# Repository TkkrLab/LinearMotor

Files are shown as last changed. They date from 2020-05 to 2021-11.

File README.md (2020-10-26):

# DIY Ironless Linear Motor
Brushless DC (BLDC) motors constist of a stator and a rotor, which produce a rotational torque when powered. A linear motor is essentially a BLDC motor which has been folded open and produces a linear force by applying current to the different phases. This causes the [forcer](#forcer) (rotor) to move along a [magnetic track](#magnetic-track) (stator).
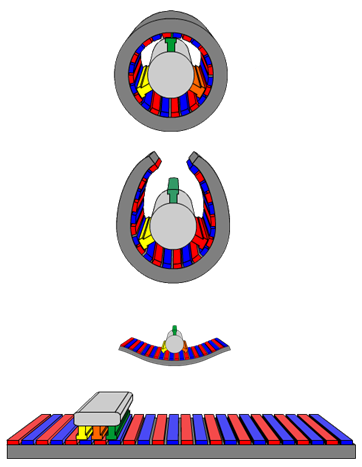
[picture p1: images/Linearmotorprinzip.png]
LinearMotorPrincipal


## Linear Motor basics
As explained a linear motor is a flattened BLDC motor. There are several different types, each having its own advantages and disadvantages. We decided to go with an ironless linear motor.
An ironless linear motor has two main components:
* A magnetic track composed of two metal plates with magnets attached and a seperator / spacer. 
* A forcer composed of 3 copper coils, an aluminium housing, wiring and epoxy.
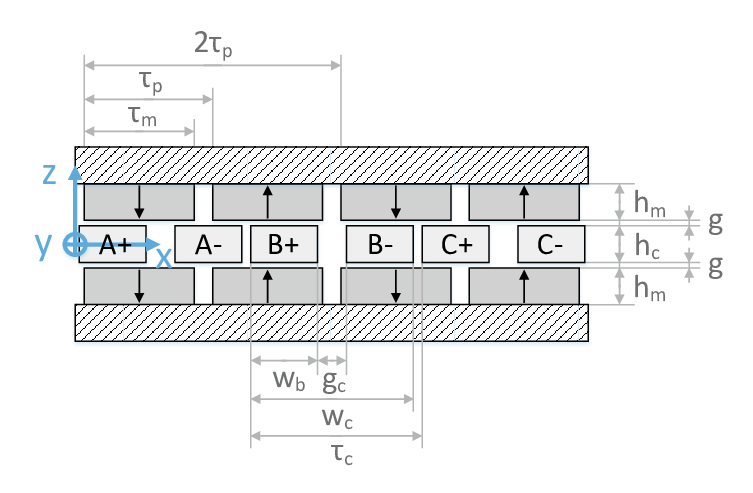
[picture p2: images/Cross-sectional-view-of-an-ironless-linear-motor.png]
CrossSection


### Magnetic Track
To get the correct spacing we take a look at a BLDC, in this case a three phase two pole motor.
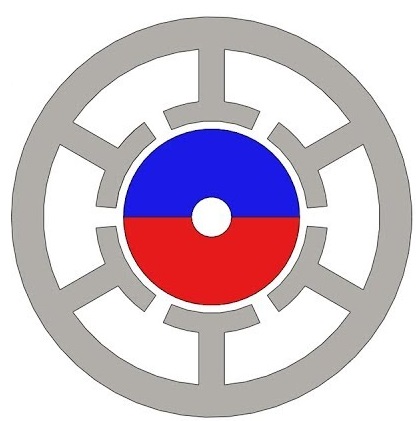
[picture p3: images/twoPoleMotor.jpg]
Three phase two pole motor


During rotation one of the phases of the motor will move from a positive polarity (+) to the negative polarity (-) and back to positive. The other two phases have a 120° offset from this phase, but for now lets focus on just the one phase. This translation in polarity means that we now know the spacing between magnets of the same polarity => 360° rotation, or 3* distance between coils(coil spacing). To get the coil spacing we take a look at what coils we have available.

The coils that we purchased were produced specifically for linear motors, they have a size of 25.5*14mm. Since we also want to add watercooling channels between the coils we decided on a spacing of 18mm. If you do not wish to add watercooling we would recommend putting the coils as close together as possible.

If we apply these values we would have a magnet with positive polarity at 0, negative polarity at 27mm and positive again at 54mm. Even though this would work, the motor will not be very powerfull. This can be improved by adding more pole pairs to the motor. You can keep adding adding pole pairs according to the following formula until you reach a magnet spacing / size suitable for your motor:  
Formula  
You can also decide on a magnet spacing first and calculate the coil spacing accordingly.

### Forcer
As previously mentioned we want to add watercooling to our linear motor so we can put more current into the coils without overheating the system. This adds some more complexity to the design of the forcer. 
For more details on the design check out [Version 1](/Solidworks/V1/README.md) and [Version 2 Watercooled](/Solidworks/V2_Watercooled/README.md)

There are some companies that sell coils made to specifications. We got ours from [JHCoils](https://www.jhcoils.com/), but if you are up to it you can always wind your own. If you decide to buy your coils, just keep in mind that you will have to pay extra if they do not have the required tooling available (So ask which sizes they have available already and pick one of those).
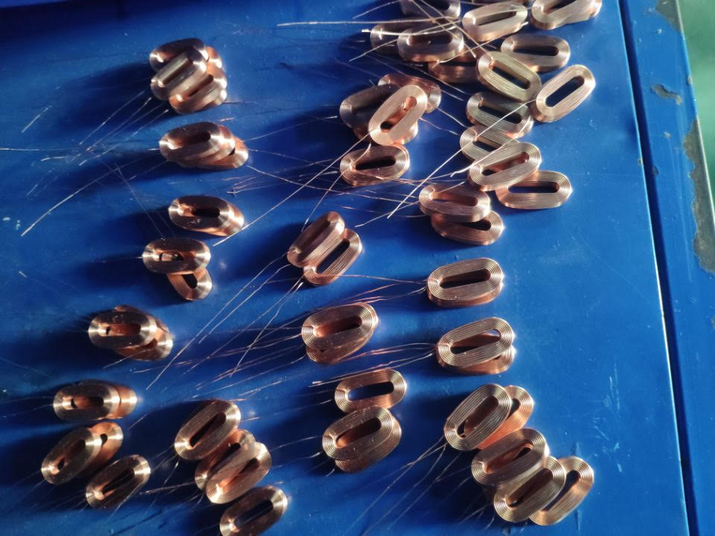
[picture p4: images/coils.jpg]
Coils


#### Coil specs
dimensions: 25.5*14 mm  
wire: 0.4mm

## Commutation
Commutation is the process of switching current in the motor phases to generate motion. Our ironless linear motors is based on a three phase motor design. There are several different ways to commutate a three phase motor, of which sinusoidal control is the most efficient and most commonly used in the higher-end motor drives. 

In sinusoidal commutation, all three wires are permanently energized with a sinusoidal current that is 120 degrees apart on each phase. This has the effect of creating a North/South magnetic field that rotates inside the motor cage. As shown in the figure below:  
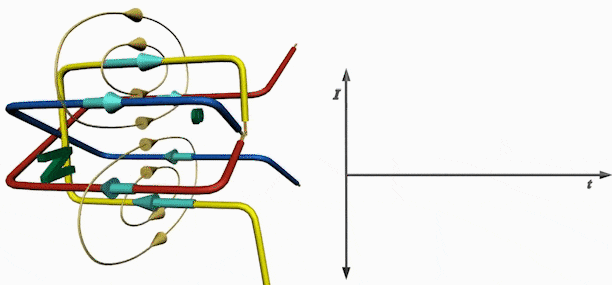
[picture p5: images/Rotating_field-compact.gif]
Commutation


If a magnet is placed on a rotor inside this cage, its North and South poles will be pulled towards the South and North poles of the rotating field. Assuming for a moment that the magnetis field rotation is paused, we can see the effect of the pull on the magnet at different angular position relative to the rotating field.

### FOC (Field Oriented Control)
...TODO...  
(https://www.roboteq.com/technology/field-oriented-control)

### Motor Drive
To drive our motor we are using a [TMC4671](https://www.trinamic.com/products/integrated-circuits/details/tmc4671-es/) controller from [Trinamic](#sponsors)

We use this drive specifically because it has hardware FOC (Field Oriented Control). The TMC4671 [datasheet](https://www.trinamic.com/fileadmin/assets/Products/ICs_Documents/TMC4671_datasheet_v1.06.pdf)  explains very well what FOC is exactly, so please check it out.

### Motor Initialization
...TODO...

__So why make our own?__
Simply, just because we can! And its awesome to learn about new stuff.

We do wish to mention [Vulcaman's](https://www.instructables.com/id/DIY-IRONLESS-LINEAR-SERVO-MOTOR/) motor build. This version is based on a simple L6234 motor controller IC and implements a basic sinusoidal commutation.

## Sponsors
We would like to thank our Trinamic for providing us with a TMC4671 evaluation kit.
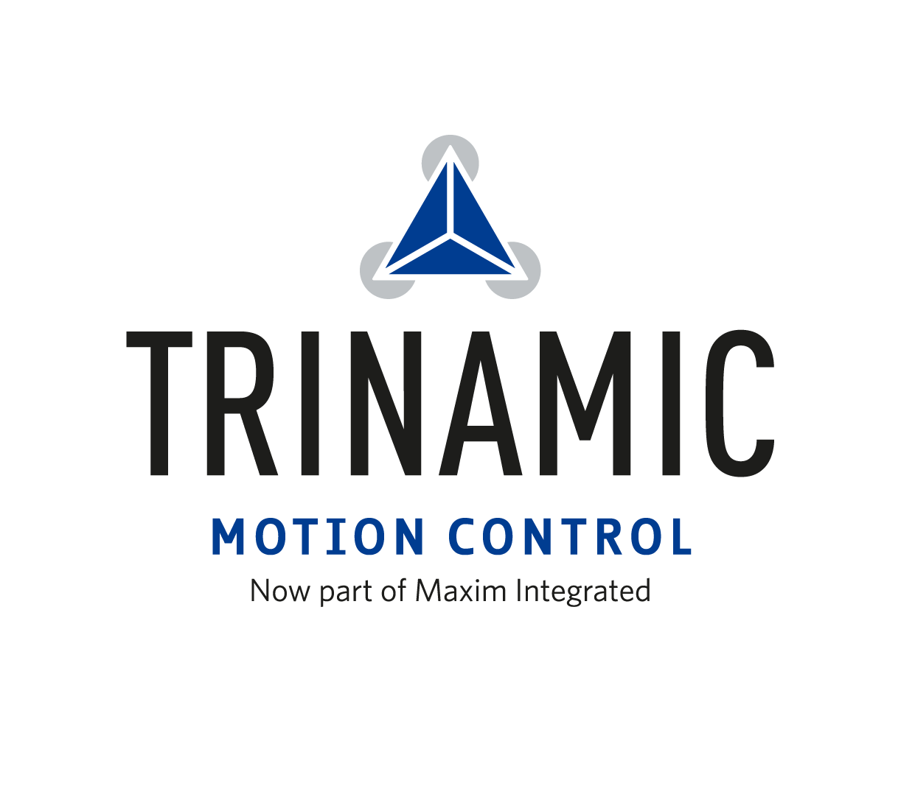
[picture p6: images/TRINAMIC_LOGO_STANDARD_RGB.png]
Trinamic


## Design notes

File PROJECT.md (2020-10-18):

---
title: "DIY Ironless Linear Motor"
date: 2020-10-03
thumbnail: "https://raw.githubusercontent.com/TkkrLab/LinearMotor/master/images/IMG_20200922_221401.jpg"
---

# DIY Ironless Linear motor
---TODO/Work in progress---

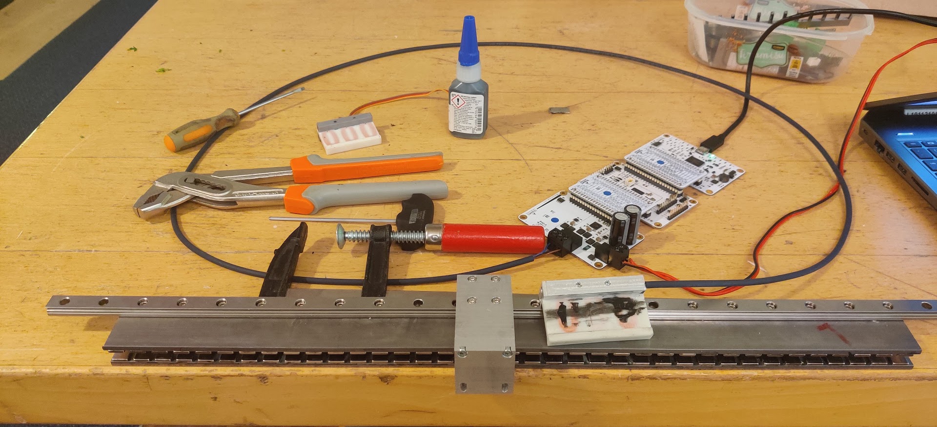
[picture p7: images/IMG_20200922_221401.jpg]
LinearMotor / LinearMotor


Check out github repository [github](https://github.com/TkkrLab/LinearMotor).

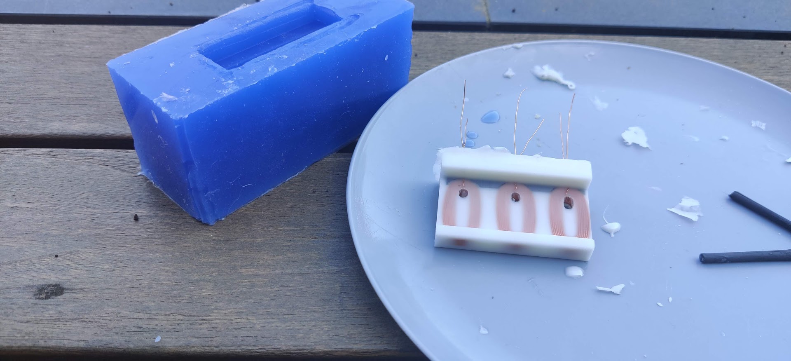
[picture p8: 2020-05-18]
images/forcer.jpg

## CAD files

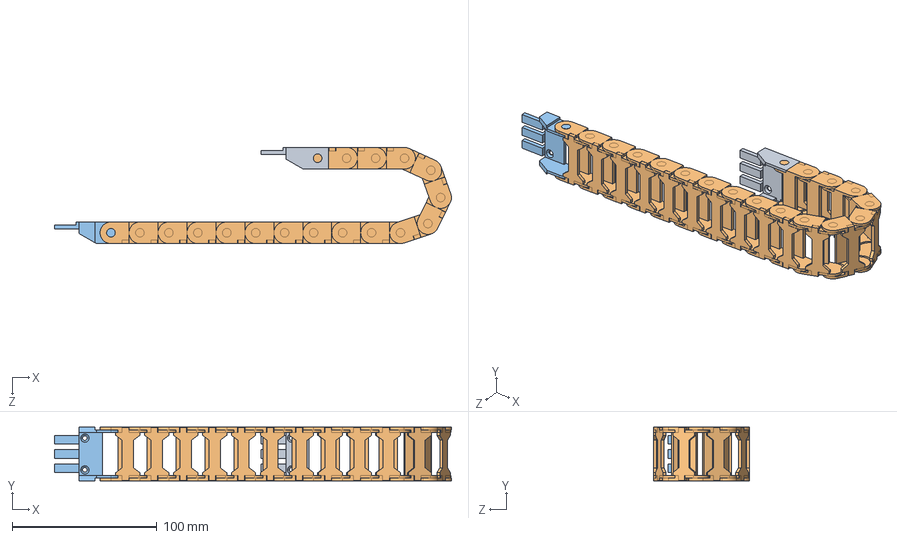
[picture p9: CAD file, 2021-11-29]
Solidworks/V2_Watercooled/Igus/chain.SLDASM
274.2 x 37.3 x 66.5 mm
0_36m_B07_30_018_0___060_30_12PZ_A1_3
0_36m_B07_30_018_0___060_30_12PZ_A1_4 x 17
0_36m_B07_30_018_0___060_30_12PZ_A1_2

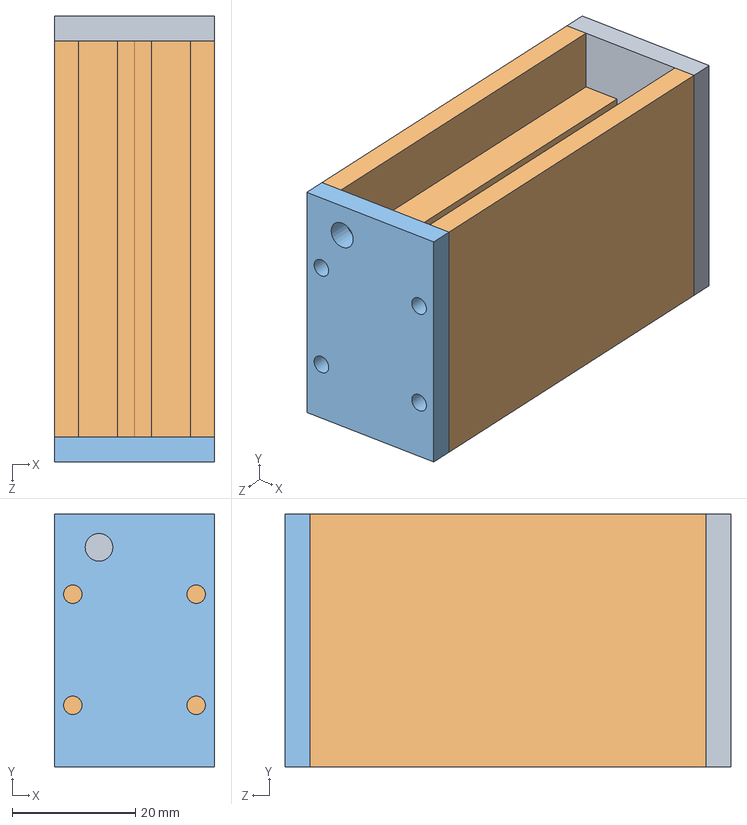
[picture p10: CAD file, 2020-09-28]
Solidworks/V2_Watercooled/CastingMould/mould.SLDASM
26.0 x 41.0 x 72.2 mm
backWall
sideWall x 2
frontWall

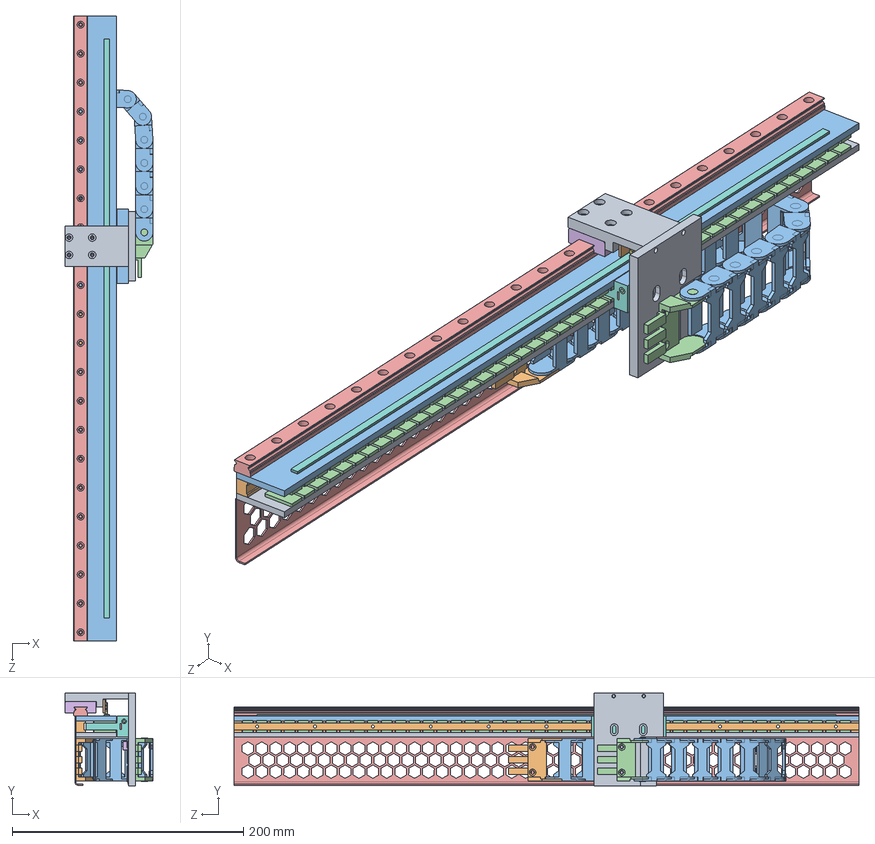
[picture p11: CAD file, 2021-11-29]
Solidworks/V2_Watercooled/LinearMotorAssembly.SLDASM
76.0 x 80.0 x 540.0 mm
enclosure_bottom
enclosure_Middle
enclosure_top
magnet_2mm x 88
MSA_012_SNS_P_MA_00
R0442_size12
RLC_3D
MS05_B-L500
connector_bracket_p1
RLC_pcb
forcer
M4 Set Screw (With Configs) x 3
spool holder
PVATube_Forcer_CoolingChannel x 2
spool x 3
forcer_printed
connector_bracket_p2
0_36m_B07_30_018_0___060_30_12PZ_A1_3
0_36m_B07_30_018_0___060_30_12PZ_A1_4 x 17
0_36m_B07_30_018_0___060_30_12PZ_A1_2
chainguide
tmc4670+tmc6100-bob

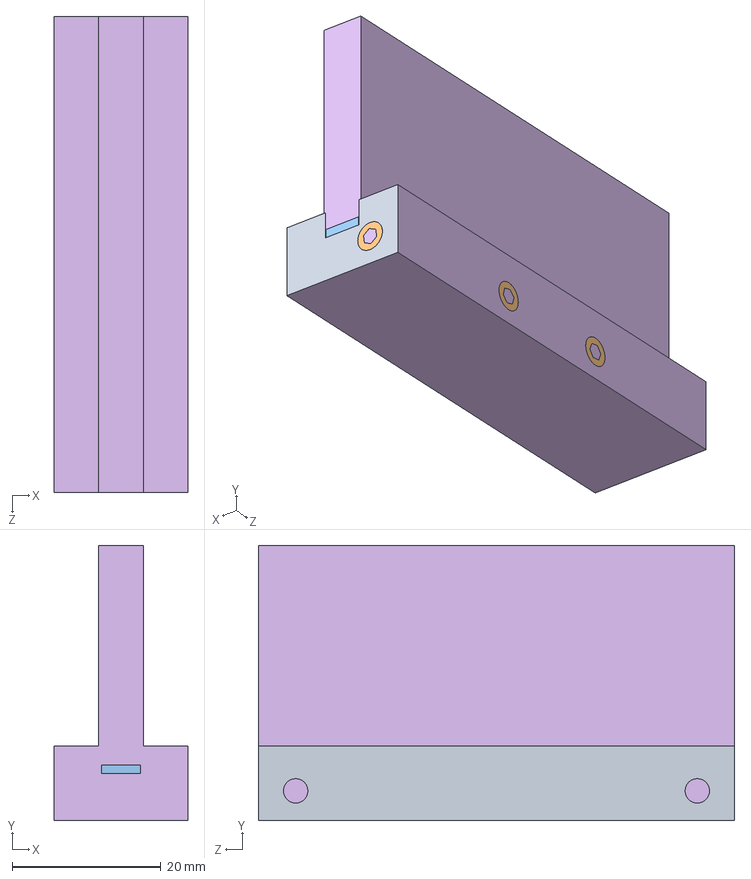
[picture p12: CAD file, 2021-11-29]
Solidworks/V2_Watercooled/forcer_assembly.SLDASM
18.0 x 37.0 x 64.0 mm
forcer
M4 Set Screw (With Configs) x 3
spool holder
PVATube_Forcer_CoolingChannel x 2
spool x 3

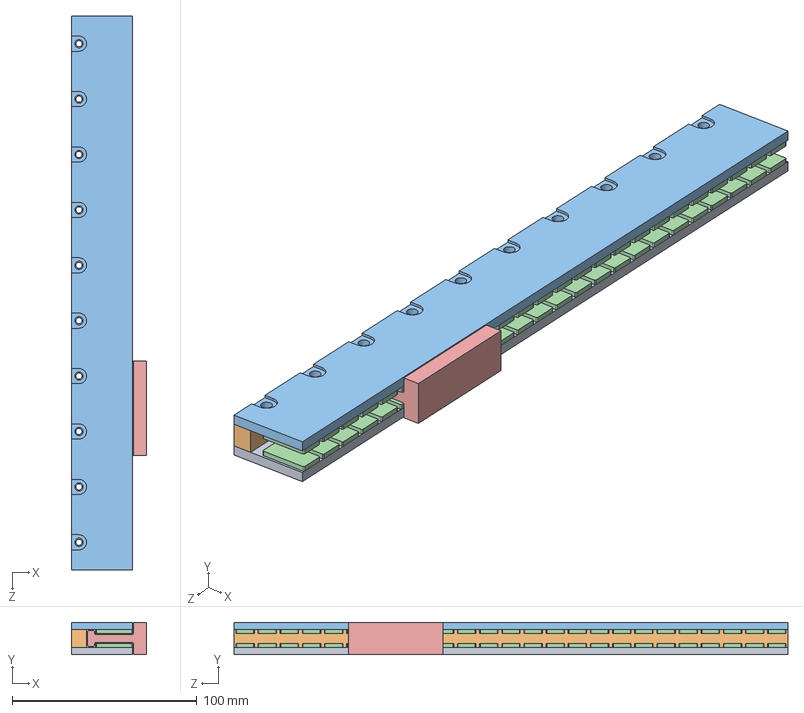
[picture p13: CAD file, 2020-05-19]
Solidworks/V1/LinearMotorAssembly.SLDASM
40.5 x 17.5 x 300.0 mm
enclosure_bottom
enclosure_Middle
enclosure_top
magnet_2mm x 50
forcer_part1

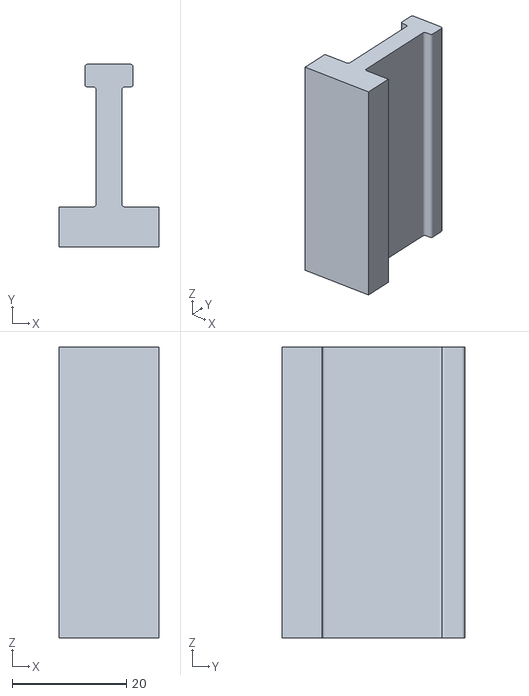
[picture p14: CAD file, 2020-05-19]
3d print STL/forcer_part1.STL
17.5 x 32.0 x 51.0

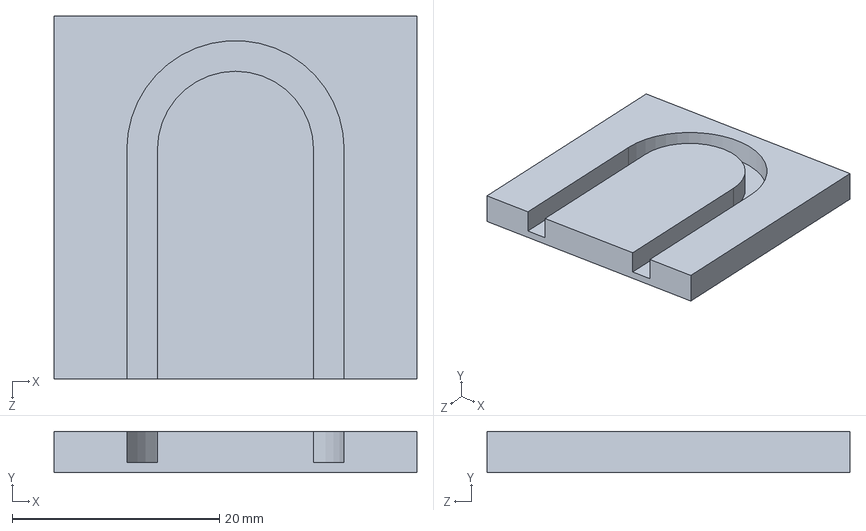
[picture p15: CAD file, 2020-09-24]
Solidworks/pva_forming_tool.SLDPRT
35.0 x 4.00 x 35.0 mm

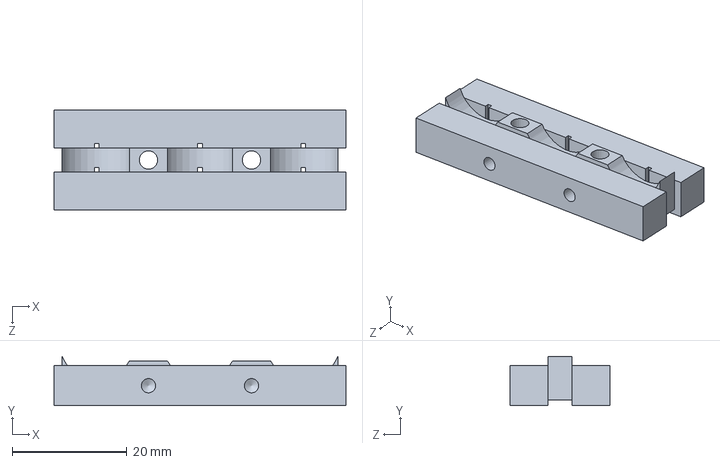
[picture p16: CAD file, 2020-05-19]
Solidworks/V1/forcer_part2.SLDPRT
51.0 x 8.64 x 17.5 mm

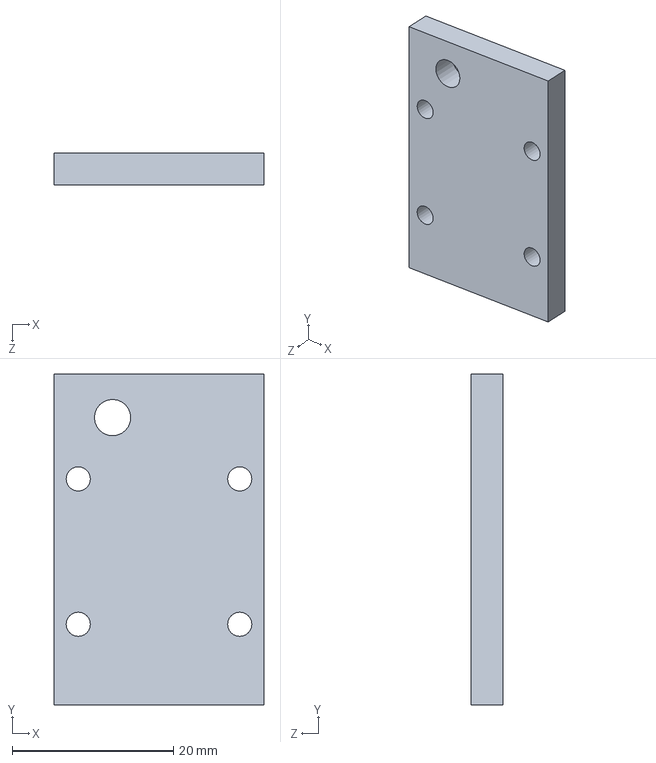
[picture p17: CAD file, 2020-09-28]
Solidworks/V2_Watercooled/CastingMould/frontWall.SLDPRT
26.0 x 41.0 x 4.00 mm

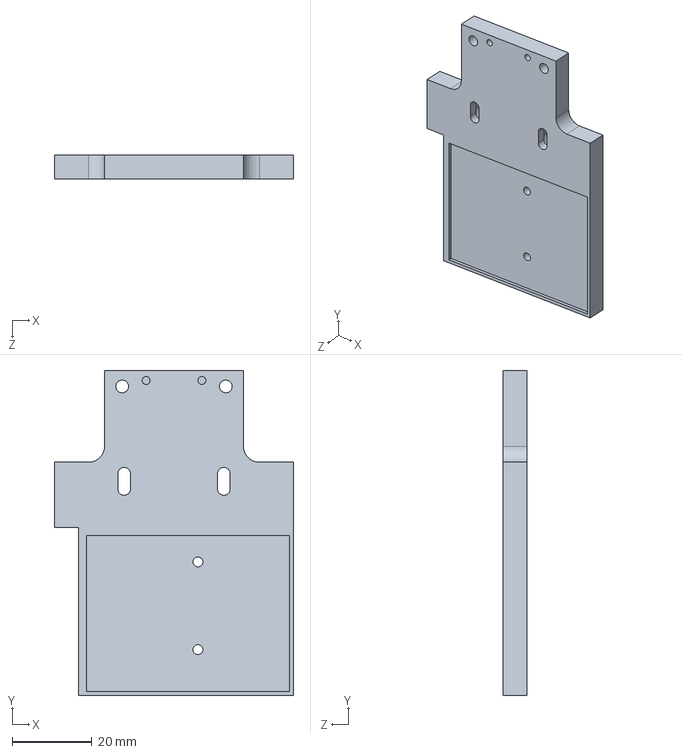
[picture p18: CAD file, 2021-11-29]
Solidworks/V2_Watercooled/connector_bracket_p2.SLDPRT
60.0 x 81.5 x 6.00 mm

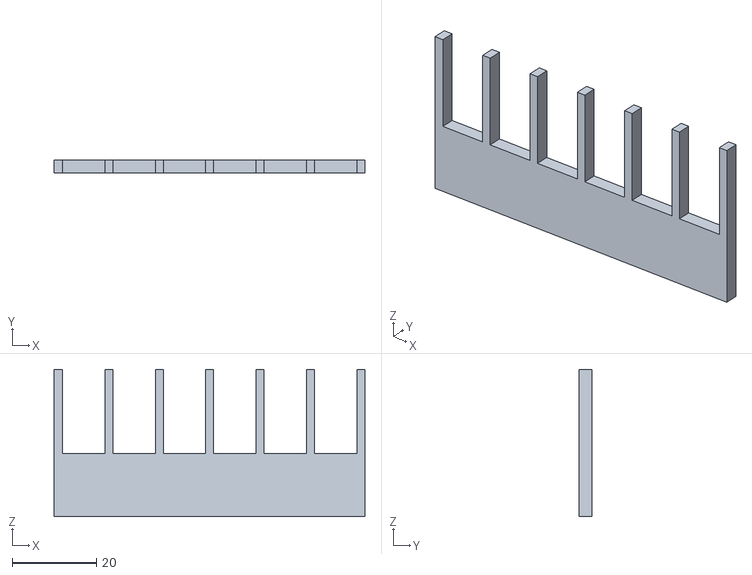
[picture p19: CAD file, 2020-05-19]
3d print STL/magnet_spacer.STL
74.0 x 3.00 x 35.0

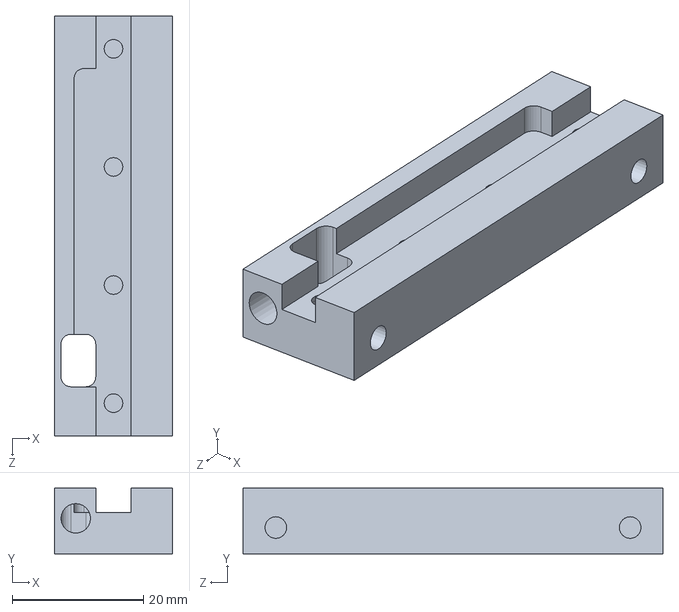
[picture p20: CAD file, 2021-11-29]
Solidworks/V2_Watercooled/forcer.SLDPRT
18.0 x 10.0 x 64.0 mm

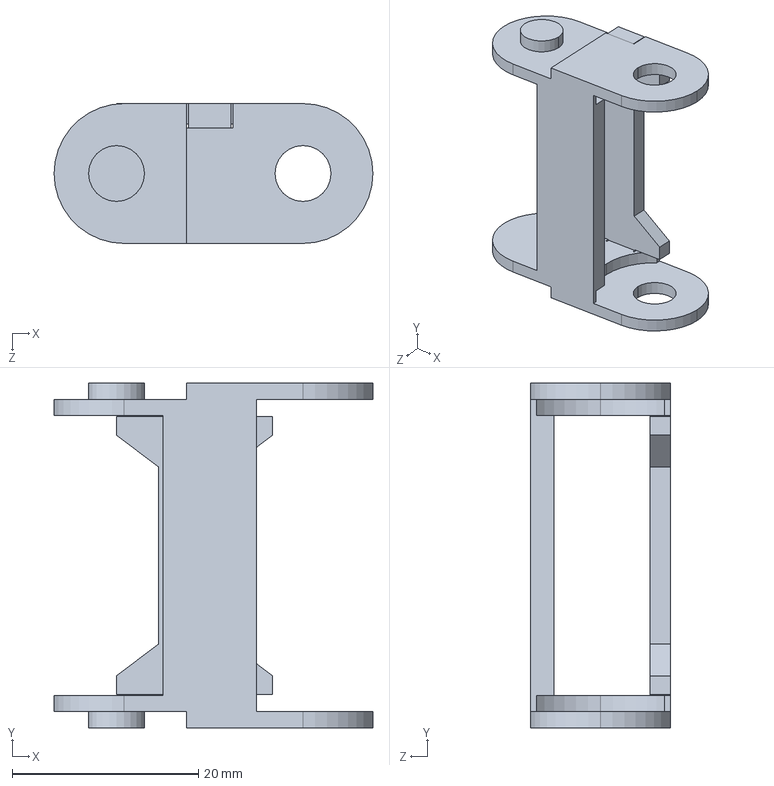
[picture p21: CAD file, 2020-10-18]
Solidworks/V2_Watercooled/Igus/0_36m_B07_30_018_0___060_30_12PZ_A1_4.SLDPRT
34.2 x 37.0 x 15.0 mm

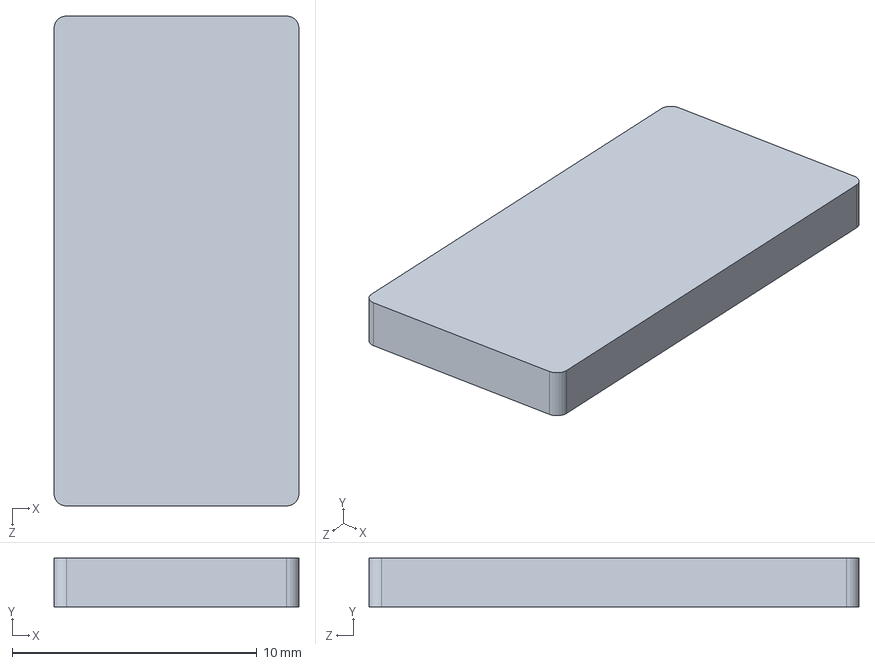
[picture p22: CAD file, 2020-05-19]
Solidworks/V1/magnet_2mm.SLDPRT
10.0 x 2.00 x 20.0 mm

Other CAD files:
Solidworks/V1/magnet_spacer.SLDPRT
3d print STL/forcer_part2.STL
Solidworks/V2_Watercooled/CastingMould/backWall.SLDPRT
Solidworks/V2_Watercooled/enclosure_top.SLDPRT
Solidworks/V1/enclosure_Middle.SLDPRT
Solidworks/V1/enclosure_bottom.SLDPRT
Solidworks/V1/enclosure_top.SLDPRT
Solidworks/V1/forcer_part1.SLDPRT
Solidworks/V2_Watercooled/CastingMould/sideWall.SLDPRT
Solidworks/V2_Watercooled/CoolingChannel.SLDPRT
Solidworks/V2_Watercooled/Igus/0_36m_B07_30_018_0___060_30_12PZ_A1_2.SLDPRT
Solidworks/V2_Watercooled/Igus/0_36m_B07_30_018_0___060_30_12PZ_A1_3.SLDPRT
Solidworks/V2_Watercooled/Igus/chainpath.SLDPRT
Solidworks/V2_Watercooled/M4 Set Screw.SLDPRT
Solidworks/V2_Watercooled/MS05B-L500.SLDPRT
Solidworks/V2_Watercooled/MSA_012_SNS_P_MA_00.SLDPRT
Solidworks/V2_Watercooled/R0442_size12.SLDPRT
Solidworks/V2_Watercooled/RLC2HD.SLDPRT
Solidworks/V2_Watercooled/RLC2HD_pcb.SLDPRT
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

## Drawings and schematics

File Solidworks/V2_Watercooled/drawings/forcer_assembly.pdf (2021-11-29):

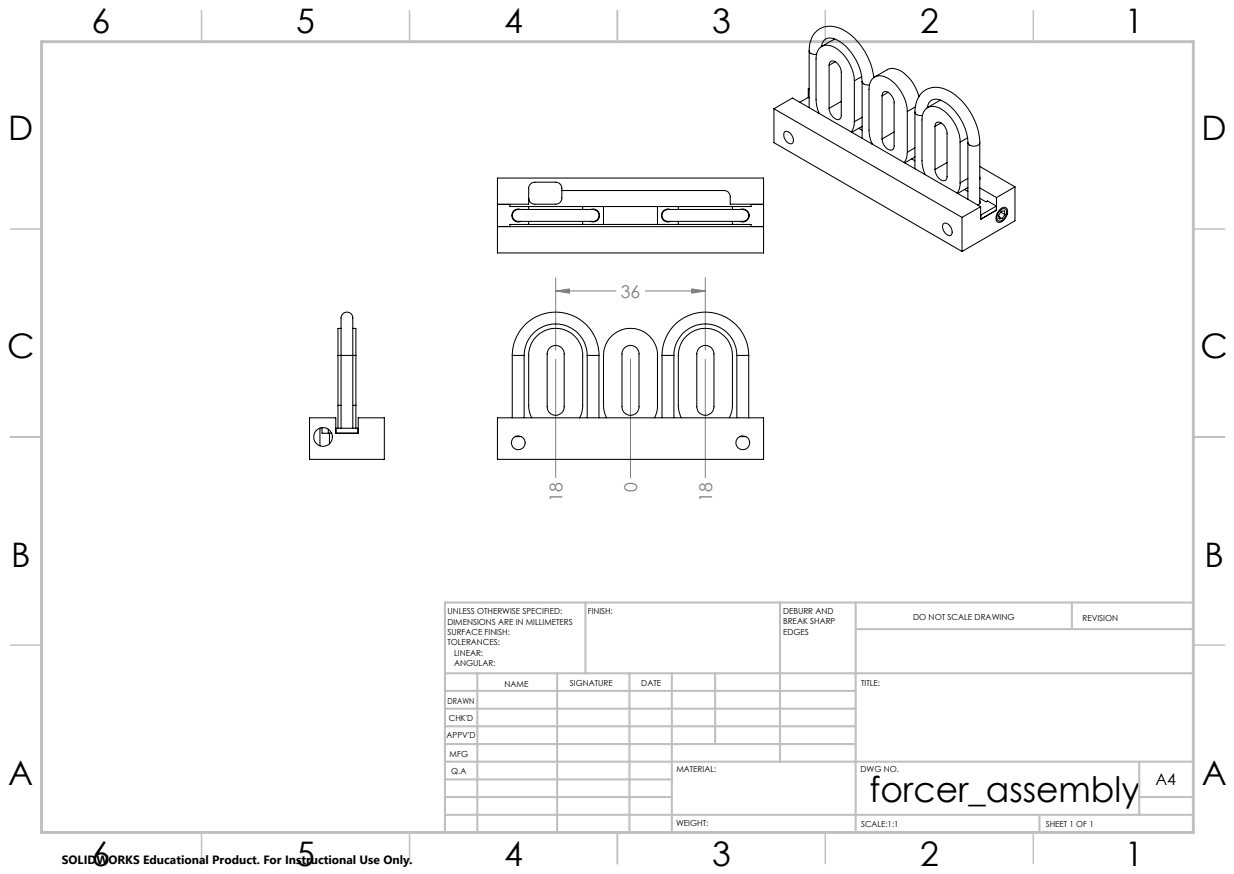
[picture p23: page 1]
FINISH:; DEBURR AND; BREAK SHARP; DO NOT SCALE DRAWING; REVISION; SCALE:1:1; SHEET 1 OF 1

UNLESS OTHERWISE SPECIFIED:
DIMENSIONS ARE IN MILLIMETERS
SURFACE FINISH:
TOLERANCES:
LINEAR:
ANGULAR:

NAME | SIGNATURE | DATE | | | | TITLE:

DRAWN
CHK'D
APPV'D
MFG
Q.A | | | | MATERIAL: | DWG NO. forcer_assembly | A4

SOLIDWORKS Educational Product. For Instructional Use Only.

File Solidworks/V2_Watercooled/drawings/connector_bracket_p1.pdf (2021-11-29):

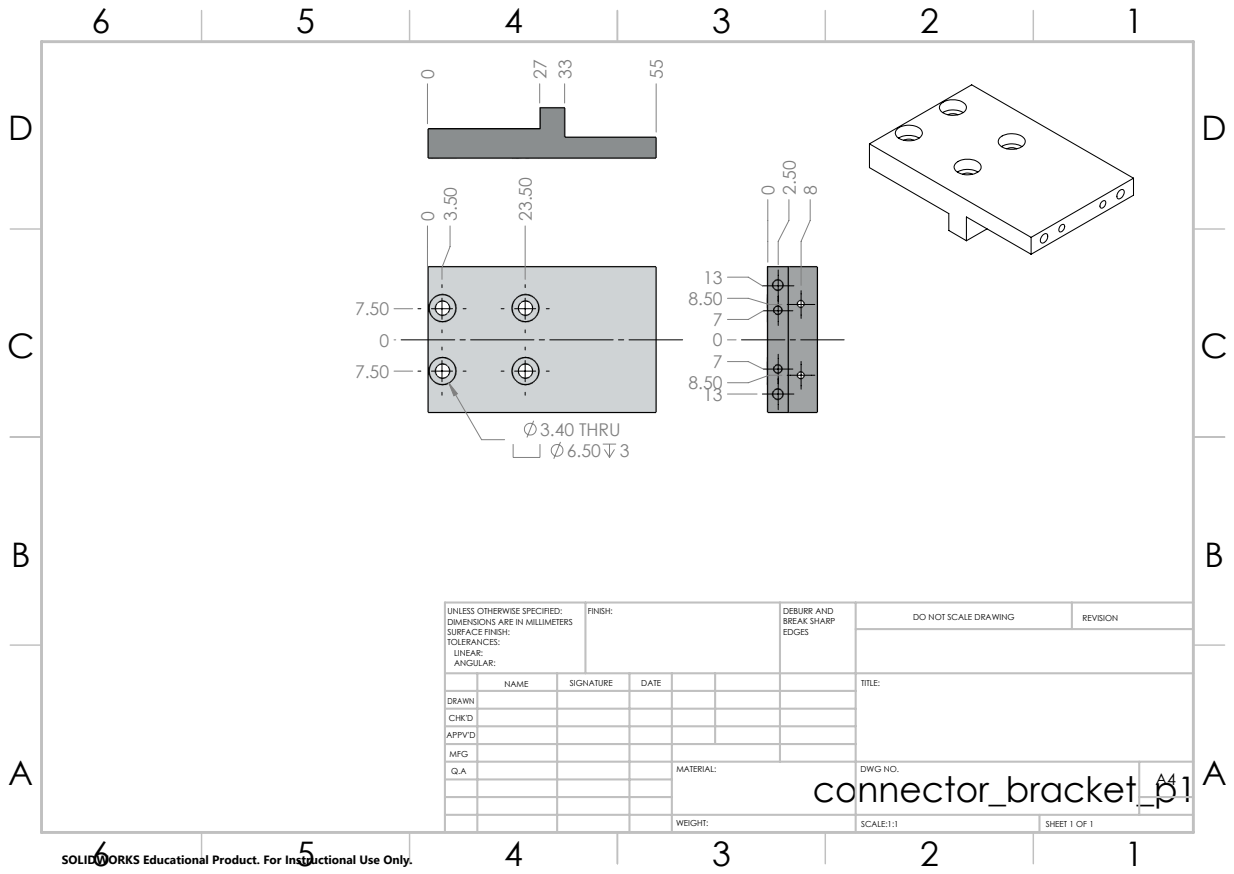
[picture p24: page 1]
3.40 THRU 6.50 3; FINISH:; DEBURR AND; BREAK SHARP; DO NOT SCALE DRAWING; REVISION; SCALE:1:1; SHEET 1 OF 1

UNLESS OTHERWISE SPECIFIED:
DIMENSIONS ARE IN MILLIMETERS
SURFACE FINISH:
TOLERANCES:
LINEAR:
ANGULAR:

NAME | SIGNATURE | DATE | | | | TITLE:

DRAWN
CHK'D
APPV'D
MFG
Q.A | | | | MATERIAL: connector_bracket_p1 | DWG NO. | A4

SOLIDWORKS Educational Product. For Instructional Use Only.

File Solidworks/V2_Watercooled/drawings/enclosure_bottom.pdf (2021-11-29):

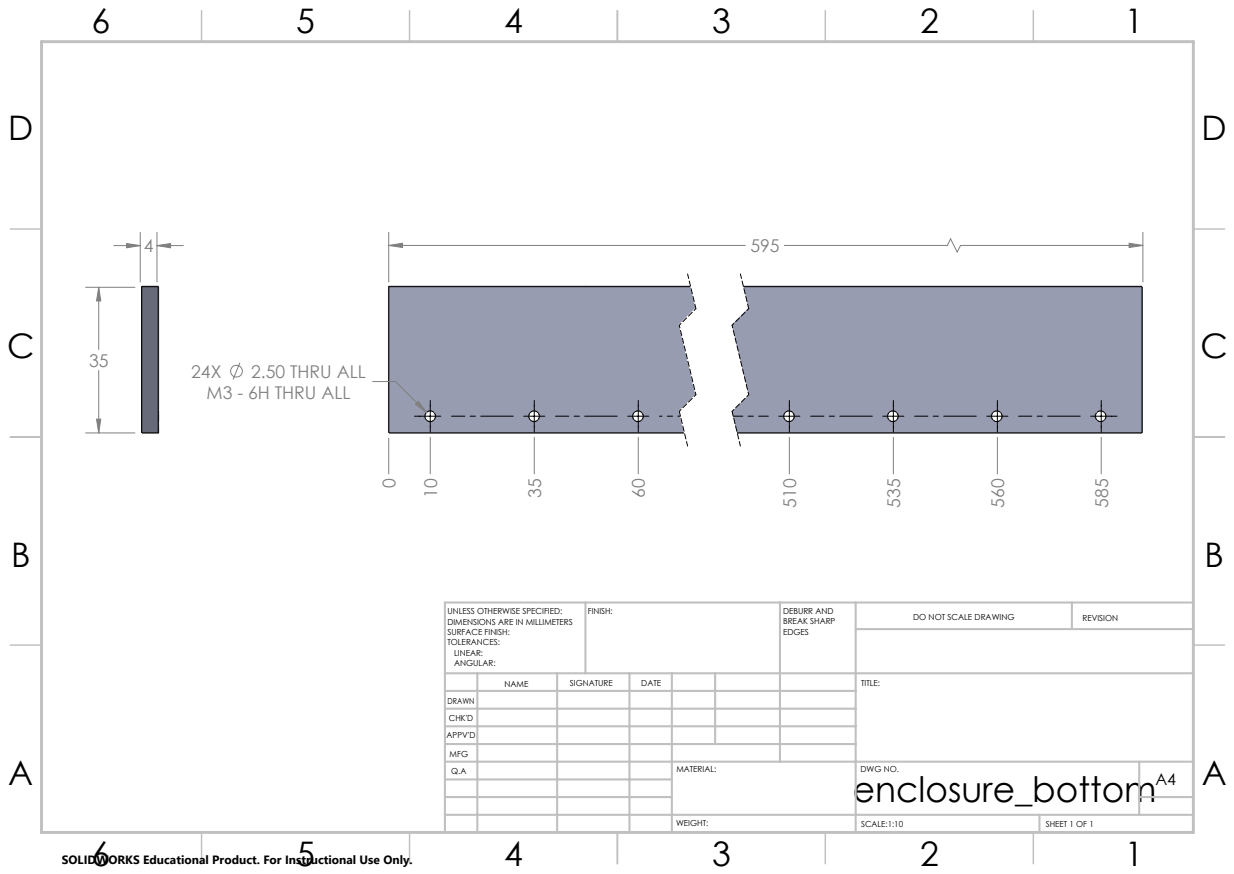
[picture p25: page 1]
2.50 THRU ALL; M3 - 6H THRU ALL; FINISH:; DEBURR AND; BREAK SHARP; DO NOT SCALE DRAWING; REVISION; SCALE:1:10; SHEET 1 OF 1

UNLESS OTHERWISE SPECIFIED:
DIMENSIONS ARE IN MILLIMETERS
SURFACE FINISH:
TOLERANCES:
LINEAR:
ANGULAR:

NAME | SIGNATURE | DATE | | | | TITLE:

DRAWN
CHK'D
APPV'D
MFG
Q.A | | | | MATERIAL: | DWG NO. enclosure_bottom | A4

SOLIDWORKS Educational Product. For Instructional Use Only.

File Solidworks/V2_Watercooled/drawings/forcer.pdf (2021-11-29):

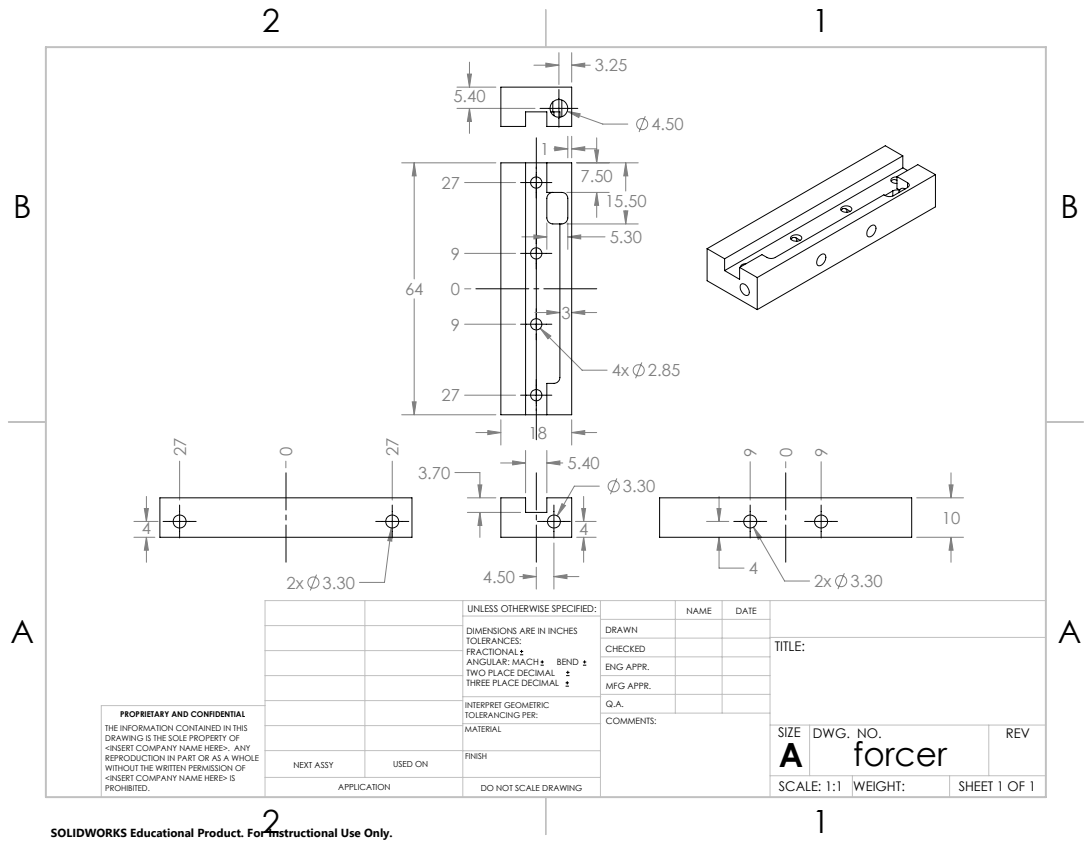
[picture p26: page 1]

UNLESS OTHERWISE SPECIFIED: | | NAME | DATE
DIMENSIONS ARE IN INCHES TOLERANCES: FRACTIONAL ANGULAR: MACH BEND TWO PLACE DECIMAL THREE PLACE DECIMAL | DRAWN

CHECKED | | | TITLE:

ENG APPR.
MFG APPR.

INTERPRET GEOMETRIC TOLERANCING PER: | Q.A.
MATERIAL | | SIZE A | DWG. NO. forcer | REV

PROPRIETARY AND CONFIDENTIAL
THE INFORMATION CONTAINED IN THIS
DRAWING IS THE SOLE PROPERTY OF
<INSERT COMPANY NAME HERE>. ANY
REPRODUCTION IN PART OR AS A WHOLE
WITHOUT THE WRITTEN PERMISSION OF
<INSERT COMPANY NAME HERE> IS
PROHIBITED.

NEXT ASSY | USED ON | FINISH

APPLICATION | DO NOT SCALE DRAWING | | SCALE: 1:1 | WEIGHT: | SHEET 1 OF 1

SOLIDWORKS Educational Product. For Instructional Use Only.

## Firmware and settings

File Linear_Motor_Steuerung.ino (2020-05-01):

#include <PID_v1.h>

#define ENC_A 2
#define ENC_B 3

volatile int encoder0Pos = 0;

#define EN1 5
#define EN2 6
#define EN3 7
 
#define IN1 9
#define IN2 10
#define IN3 11

#define DirPin 4
#define StepPin 12

double Setpoint, Input, Output;
PID myPID(&Input, &Output, &Setpoint,2,5,1, DIRECT);

// SPWM (Sine Wave)
//const int pwmSin[72] = {127, 138, 149, 160, 170, 181, 191, 200, 209, 217, 224, 231, 237, 242, 246, 250, 252, 254, 254, 254, 252, 250, 246, 242, 237, 231, 224, 217, 209, 200, 191, 181, 170, 160, 149, 138, 127, 116, 105, 94, 84, 73, 64, 54, 45, 37, 30, 23, 17, 12, 8, 4, 2, 0, 0, 0, 2, 4, 8, 12, 17, 23, 30, 37, 45, 54, 64, 73, 84, 94, 105, 116 };

// SVPWM (Space Vector Wave)
const int pwmSin[] = {128, 132, 136, 140, 143, 147, 151, 155, 159, 162, 166, 170, 174, 178, 181, 185, 189, 192, 196, 200, 203, 207, 211, 214, 218, 221, 225, 228, 232, 235, 238, 239, 240, 241, 242, 243, 244, 245, 246, 247, 248, 248, 249, 250, 250, 251, 252, 252, 253, 253, 253, 254, 254, 254, 255, 255, 255, 255, 255, 255, 255, 255, 255, 255, 255, 255, 255, 254, 254, 254, 253, 253, 253, 252, 252, 251, 250, 250, 249, 248, 248, 247, 246, 245, 244, 243, 242, 241, 240, 239, 238, 239, 240, 241, 242, 243, 244, 245, 246, 247, 248, 248, 249, 250, 250, 251, 252, 252, 253, 253, 253, 254, 254, 254, 255, 255, 255, 255, 255, 255, 255, 255, 255, 255, 255, 255, 255, 254, 254, 254, 253, 253, 253, 252, 252, 251, 250, 250, 249, 248, 248, 247, 246, 245, 244, 243, 242, 241, 240, 239, 238, 235, 232, 228, 225, 221, 218, 214, 211, 207, 203, 200, 196, 192, 189, 185, 181, 178, 174, 170, 166, 162, 159, 155, 151, 147, 143, 140, 136, 132, 128, 124, 120, 116, 113, 109, 105, 101, 97, 94, 90, 86, 82, 78, 75, 71, 67, 64, 60, 56, 53, 49, 45, 42, 38, 35, 31, 28, 24, 21, 18, 17, 16, 15, 14, 13, 12, 11, 10, 9, 8, 8, 7, 6, 6, 5, 4, 4, 3, 3, 3, 2, 2, 2, 1, 1, 1, 1, 1, 1, 1, 1, 1, 1, 1, 1, 1, 2, 2, 2, 3, 3, 3, 4, 4, 5, 6, 6, 7, 8, 8, 9, 10, 11, 12, 13, 14, 15, 16, 17, 18, 17, 16, 15, 14, 13, 12, 11, 10, 9, 8, 8, 7, 6, 6, 5, 4, 4, 3, 3, 3, 2, 2, 2, 1, 1, 1, 1, 1, 1, 1, 1, 1, 1, 1, 1, 1, 2, 2, 2, 3, 3, 3, 4, 4, 5, 6, 6, 7, 8, 8, 9, 10, 11, 12, 13, 14, 15, 16, 17, 18, 21, 24, 28, 31, 35, 38, 42, 45, 49, 53, 56, 60, 64, 67, 71, 75, 78, 82, 86, 90, 94, 97, 101, 105, 109, 113, 116, 120, 124};

#define ARRAYSIZE sizeof(pwmSin)/sizeof(int)

enum phase {PHASE1, PHASE2, PHASE3};
int phasePwmIndex[3];

int *pos_U, *pos_V, *pos_W;

int commutationPWMOffset = 24;

//This distance is the difference between two magnets with the same polarity.
const double phaseDistance = 27;

double position_in_mm = 0; // (encoder0Pos) / 40.00;
String inString = "";

void setup() 
{
  commutationPWMOffset = ARRAYSIZE/3;

  phasePwmIndex[0] = 0;
  phasePwmIndex[1] = commutationPWMOffset;
  phasePwmIndex[2] = (2*commutationPWMOffset);
  
  *pos_U = pwmSin + phasePwmIndex[0];
  *pos_V = pwmSin + phasePwmIndex[1];
  *pos_W = pwmSin + phasePwmIndex[2];

  pinMode(ENC_A, INPUT);
  pinMode(ENC_B, INPUT);

  attachInterrupt(0, isrA, CHANGE);
  attachInterrupt(1, isrB, CHANGE);

  //Increase PWM frequency to 32 kHz  (make inaudible)
  setPwmFrequency(IN1);
  setPwmFrequency(IN2);
  setPwmFrequency(IN3);

  pinMode(IN1, OUTPUT); 
  pinMode(IN2, OUTPUT); 
  pinMode(IN3, OUTPUT); 
  pinMode(EN1, OUTPUT); 
  pinMode(EN2, OUTPUT); 
  pinMode(EN3, OUTPUT); 
 
 
  digitalWrite(EN1, HIGH);
  digitalWrite(EN2, HIGH);
  digitalWrite(EN3, HIGH);

  analogWrite(IN1,*pos_U);
  analogWrite(IN2,*pos_V);
  analogWrite(IN3,*pos_W);
  
  //wait for 2 seconds for forcer to settle in position
  delay(2000);

  encoder0Pos = 0;
  
  analogWrite(IN1,0);
  analogWrite(IN2,0);
  analogWrite(IN3,0);

  myPID.SetOutputLimits(-1000, 1000);
  myPID.SetMode(AUTOMATIC);
  myPID.SetSampleTime(1);
  myPID.SetTunings(15,0,0.4);
  Serial.begin(115200);
}



void loop()
{
  //Read Setpoint from serial communication
  if(Serial.available() > 0)
  {
    int inChar = Serial.read();
    if (isDigit(inChar))
    {
      inString += (char)inChar;
    }
    if (inChar == '\n')
    {
      Setpoint = inString.toInt();
      Serial.print("SetPoint");
      Serial.println(Setpoint);
      inString = "";
    }
  }
  Input = encoder0Pos / 40.00;
  myPID.Compute();
  drive(Output/1000);
}

void drive(double scale_factor)
{
  if(scale_factor < 0.00)
  {
    //linear scale Y = x * (ymax - ymin)/(xmax - xmin) + offset
    scale_factor = (-scale_factor - 0.00) * (1.0 - 0.1) / (1.00 - 0.00) + 0.1;
    
    int offset = -(phasePwmIndex[0] - berechne() + commutationPWMOffset);
    shift(&pos_U, offset, ARRAYSIZE, PHASE1);
    shift(&pos_V, offset, ARRAYSIZE, PHASE2);
    shift(&pos_W, offset, ARRAYSIZE, PHASE3);
  
    analogWrite(IN1,*pos_U * scale_factor);
    analogWrite(IN2,*pos_V * scale_factor);
    analogWrite(IN3,*pos_W * scale_factor);
  }
  else if(scale_factor > 0.00)
  {
    scale_factor = (scale_factor - 0.00) * (1.0 - 0.1) / (1.00 - 0.00) + 0.1;
    int offset = (phasePwmIndex[0] + berechne() + commutationPWMOffset);
    shift(&pos_U, offset, ARRAYSIZE, PHASE1);
    shift(&pos_V, offset, ARRAYSIZE, PHASE2);
    shift(&pos_W, offset, ARRAYSIZE, PHASE3);
    
    analogWrite(IN1,*pos_U * scale_factor);
    analogWrite(IN2,*pos_V * scale_factor);
    analogWrite(IN3,*pos_W * scale_factor);
  }
}

int berechne()
{
  double position_in_mm = encoder0Pos / 40.00;
  int multiple = position_in_mm / phaseDistance;
  double phaseshift_mm = position_in_mm - (multiple * phaseDistance);
  return ((phaseshift_mm - 0) * (72 - 0) / (phaseDistance - 0) + 0);
}

//######################## Shift-Array########################
void shift(int **pwm_sin, int shift_distance, int array_size, phase phase_number)
{
  if(shift_distance != array_size)
  {
    if(shift_distance > 0)
    {
      if(phasePwmIndex[phase_number] + shift_distance < array_size)
      {
        *pwm_sin = *pwm_sin + shift_distance;
         phasePwmIndex[phase_number] += shift_distance;
      }
      else
      {
        int temp =phasePwmIndex[phase_number] + shift_distance - array_size;
        *pwm_sin = *pwm_sin - phasePwmIndex[phase_number];
        *pwm_sin = *pwm_sin + temp;
        phasePwmIndex[phase_number] = temp;
      }
    }
    else if(shift_distance < 0)
    {
      int temp_distance = array_size + shift_distance;
      shift(pwm_sin, temp_distance , array_size, phase_number);
    }
  }
}


//########################### ENCODER-INTERRUPT#########################################
void isrA()
{
  if (bitRead(PIND, ENC_B) != bitRead(PIND, ENC_A))
  {
    encoder0Pos++;
  }
  else
  {
    encoder0Pos--;
  }
}

void isrB()
{
  if (bitRead(PIND, ENC_A) == bitRead(PIND, ENC_B))
  {
    encoder0Pos++;
  }
  else
  {
    encoder0Pos--;
  }
}

//#################### PWM-Motor#######################
void setPwmFrequency(int pin) {
  if(pin == 5 || pin == 6 || pin == 9 || pin == 10) {
    if(pin == 5 || pin == 6) {
      TCCR0B = TCCR0B & 0b11111000 | 0x01;
    } else {
      TCCR1B = TCCR1B & 0b11111000 | 0x01;
    }
  }
  else if(pin == 3 || pin == 11) {
    TCCR2B = TCCR2B & 0b11111000 | 0x01;
  }
}

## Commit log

2020-05-01 Changed pin variables to defines. removed some unused code.
2020-05-19 Added STL and Solidworks files. Updated README
    [LinearMotorAssembly.SLDASM, enclosure_Middle.SLDPRT, enclosure_bottom.SLDPRT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]
2020-08-17 Added Watercooled V2
    [CoolingChannel.SLDPRT, LinearMotorAssembly.SLDASM, M4 Set Screw.SLDPRT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]
2020-09-24 added missing forcer part, updated forcer assembly. added casting mould
    [LinearMotorAssembly.SLDASM, backWall.SLDPRT, forcer.SLDPRT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]
2020-09-28 removed h-shape design in favor of t-shape to reduce cast complexity.
    [backWall.SLDPRT, forcer_assembly.SLDASM, forcer_printed.SLDPRT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]
2020-10-18 Added Igus cablechain.
    [0_36m_B07_30_018_0___060_30_12PZ_A1_2.SLDPRT, 0_36m_B07_30_018_0___060_30_12PZ_A1_3.SLDPRT, 0_36m_B07_30_018_0___060_30_12PZ_A1_4.SLDPRT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]
2020-12-29 Added drawings and step file of complete assembly.
    [connector_bracket_p1.SLDDRW, connector_bracket_p2.SLDDRW, connector_bracket_p2.SLDPRT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]
2021-09-10 latest changes
    [LinearMotorAssembly.SLDASM, MSA_012_SNS_P_MA_00.SLDPRT, chain.SLDASM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]
